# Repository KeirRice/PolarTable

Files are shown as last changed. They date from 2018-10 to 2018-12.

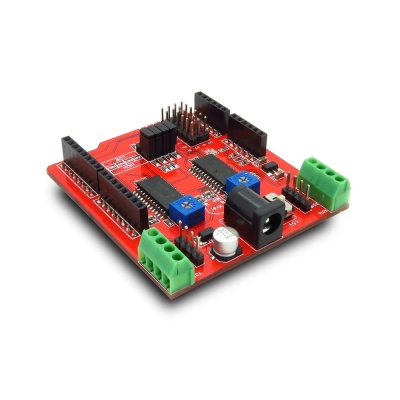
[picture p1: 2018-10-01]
Documents/Motor Shield/400px-ITEAD_DUAL_STEP_MOTOR_DRIVER_SHIELD.jpg

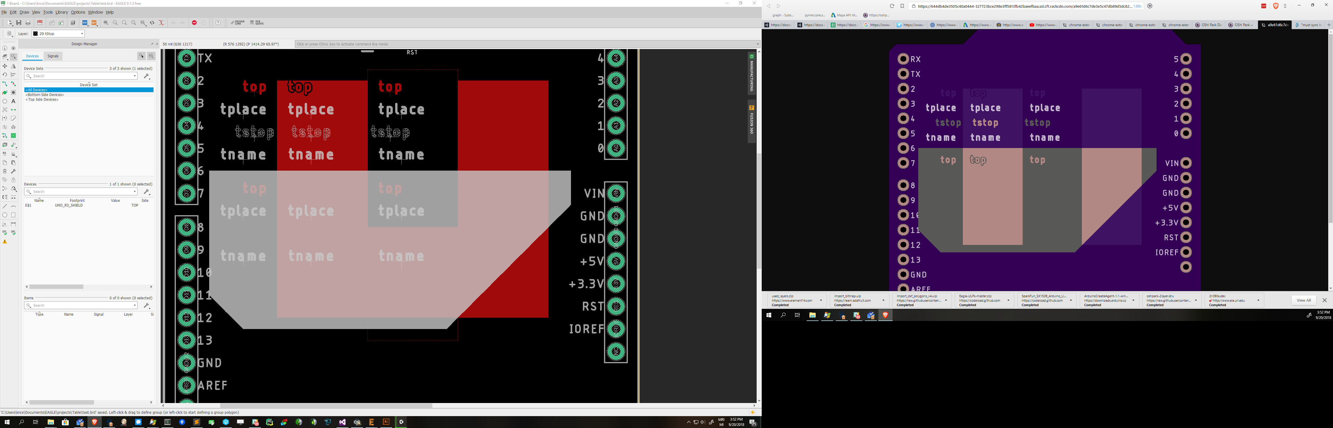
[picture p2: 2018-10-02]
Eagle/Images/Image 416.png

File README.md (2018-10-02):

# PolarTable

A colletion of design, code and art that is my journey towards making a physical table with a polor plotting system build in.

<p align="center">
  Polar Table Logo consisting of three rings braided togeather. Polar Table Logo
</p>

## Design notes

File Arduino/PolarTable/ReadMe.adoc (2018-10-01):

:Author: keir
:Email: keirrice@gmail.com
:Date: 18/09/2018
:Revision: version#
:License: Public Domain

= Project: {Project}

Describe your project

== Step 1: Installation
Please describe the steps to install this project.

For example:

1. Open this file
2. Edit as you like
3. Release to the World!

== Step 2: Assemble the circuit

Assemble the circuit following the diagram layout.png attached to the sketch

== Step 3: Load the code

Upload the code contained in this sketch on to your board

=== Folder structure

....
 sketch123                => Arduino sketch folder
  ├── sketch123.ino       => main Arduino file
  ├── schematics.png      => (optional) an image of the required schematics
  ├── layout.png          => (optional) an image of the layout
  └── ReadMe.adoc         => this file
....

=== License
This project is released under a {License} License.

=== Contributing
To contribute to this project please contact keir <keirrice@gmail.com>

=== BOM
Add the bill of the materials you need for this project.

|===
| ID | Part name      | Part number | Quantity
| R1 | 10k Resistor   | 1234-abcd   | 10       
| L1 | Red LED        | 2345-asdf   | 5        
| A1 | Arduino Zero   | ABX00066    | 1        
|===

=== Help
This document is written in the _AsciiDoc_ format, a markup language to describe documents. 
If you need help you can search the http://www.methods.co.nz/asciidoc[AsciiDoc homepage]
or consult the http://powerman.name/doc/asciidoc[AsciiDoc cheatsheet]

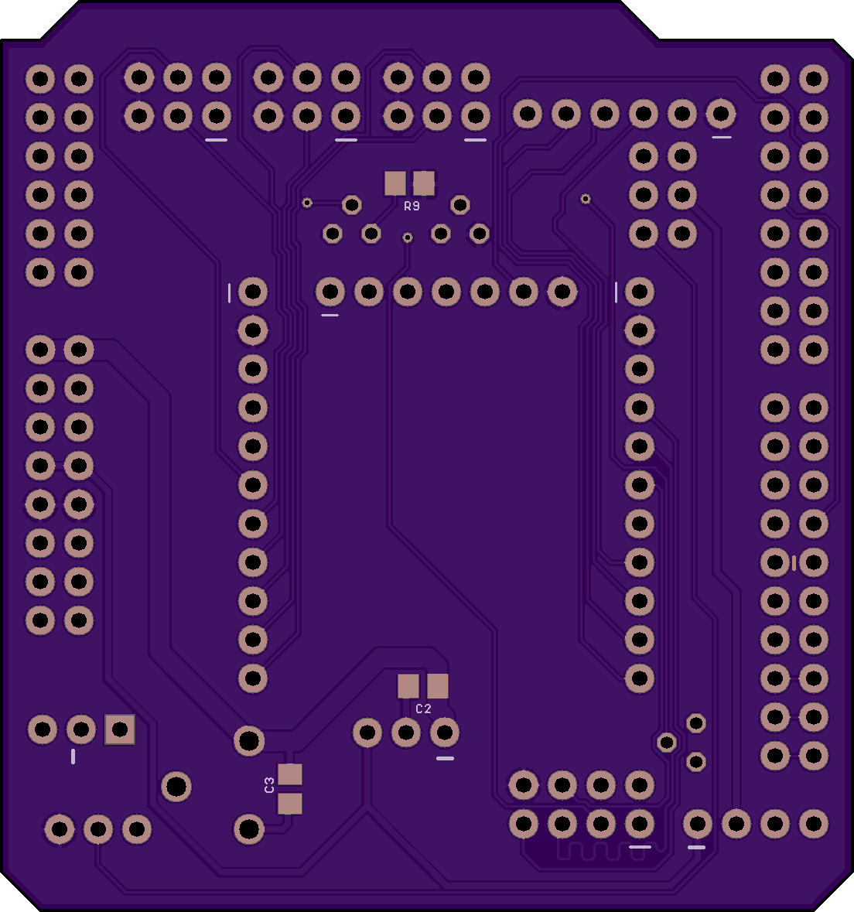
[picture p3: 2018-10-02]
Eagle/Images/0280e06795d403390924789a026d7050.png

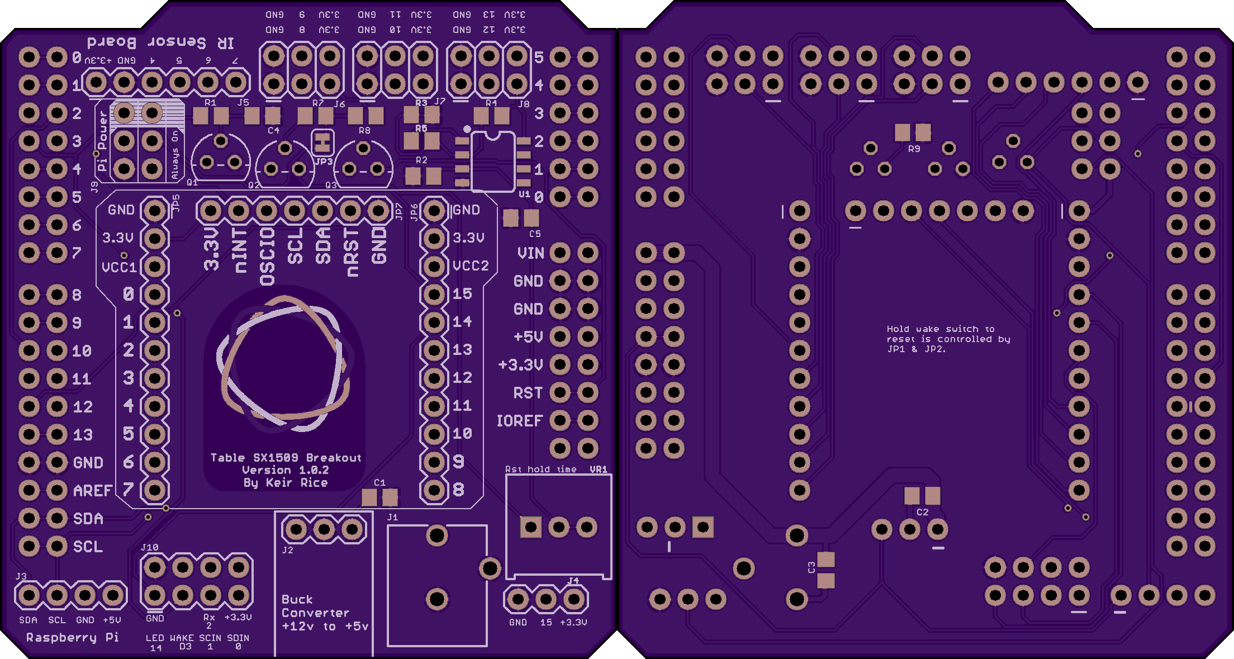
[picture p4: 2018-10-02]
Eagle/Images/72d867c8b2ec909129fff464216e762a.png

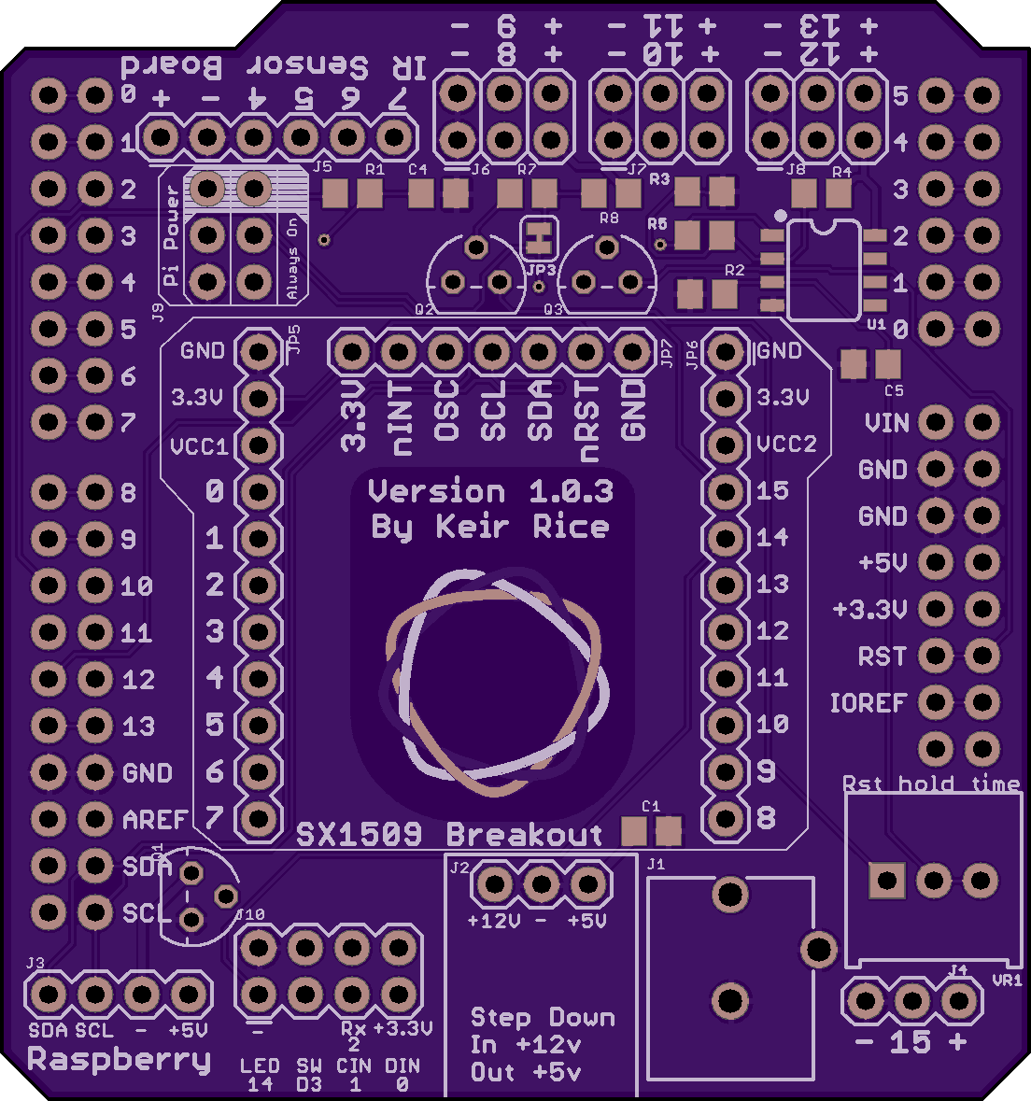
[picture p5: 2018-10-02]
Eagle/Images/a7a67751ff4bf5704754c66c1f886f41.png

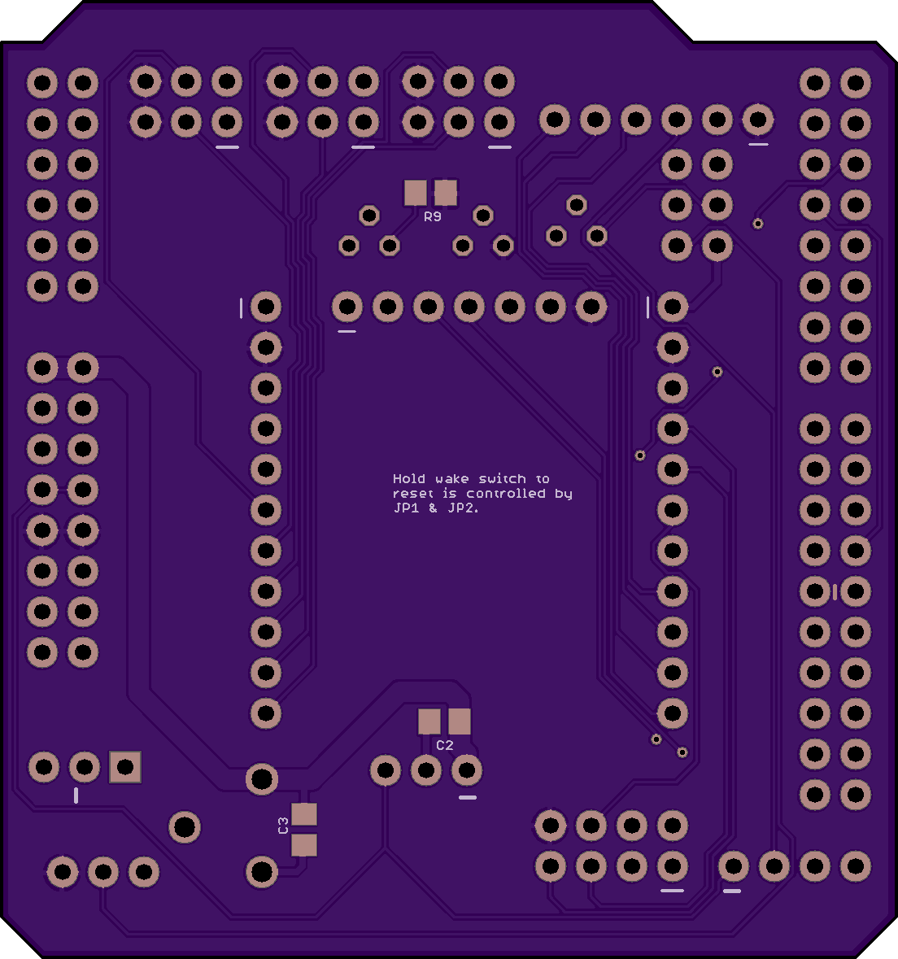
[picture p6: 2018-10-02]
Eagle/Images/8fd5240fe0b296190051bf0401c98b29 (1).png

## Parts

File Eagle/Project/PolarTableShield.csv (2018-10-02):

Part | Value | Device | Package | Description | NOTE | PROD_ID | SF_SKU | SPICEPREFIX | VALUE
B1 | Connect down to Arduino | ARDUINO_UNO_R3_SHIELDNOLABELS | UNO_R3_SHIELD_NOLABELS | Arduino R3 Shield Footprint
B2 | Connect up to motor shield | ARDUINO_UNO_R3_SHIELDNOLABELS | UNO_R3_SHIELD_NOLABELS | Arduino R3 Shield Footprint
C1 | 100u | CPOL-EUE2-5 | E2-5 | POLARIZED CAPACITOR, European symbol |  |  |  | C
C2 | 100u | CPOL-EUE2-5 | E2-5 | POLARIZED CAPACITOR, European symbol |  |  |  | C
C4 | 100nF | C-EUC0805 | C0805 | CAPACITOR, European symbol
C5 | 330uF | C-EUC0805 | C0805 | CAPACITOR, European symbol
C9 | 100n | C-EUC0805 | C0805 | CAPACITOR, European symbol |  |  |  | C
D1 | 1N5408 | 1N5408 | DO15-12 | DIODE
IC2 | LM358D | LM358D | SO08 | OP AMP also LM158; LM258; LM2904
J1 | Pi Power Jack | POWER_JACKPTH_BREAD | POWER_JACK_PTH_BREAD | Power Jack Connector |  | PRT-10811
J2 | Header - Right angled, female | CONN_031X03_2.54MM_RA_FEMALE | 1X03 | Multi connection point. Often used as Generic Header-pin footprint for 0.1 inch spaced/style header connections
J3 | Pi Connection | CONN_041X04_1.24MM_RA_MALE | 1X04_1.24MM_RA_MALE | Multi connection point. Often used as Generic Header-pin footprint for 0.1 inch spaced/style header connections
J4 |  | CONN_041X04_1.24MM_RA_MALE | 1X04_1.24MM_RA_MALE | Multi connection point. Often used as Generic Header-pin footprint for 0.1 inch spaced/style header connections
J5 | IR Sensors | CONN_06SILK_FEMALE_PTH | 1X06 | Multi connection point. Often used as Generic Header-pin footprint for 0.1 inch spaced/style header connections |  | CONN-08437
J6 | Switch A + B | CONN_03X22X03_2.54MM_RA_MALE | 2X3 | Multi connection point. Often used as Generic Header-pin footprint for 0.1 inch spaced/style header connections
J7 | Switch C + D | CONN_03X22X03_2.54MM_RA_MALE | 2X3 | Multi connection point. Often used as Generic Header-pin footprint for 0.1 inch spaced/style header connections
J8 | Switch E + F | CONN_03X22X03_2.54MM_RA_MALE | 2X3 | Multi connection point. Often used as Generic Header-pin footprint for 0.1 inch spaced/style header connections
J10 | LED + Radio | CONN_04X22X4_1.24MM_RA_MALE | 2X4 | Multi connection point. Often used as Generic Header-pin footprint for 0.1 inch spaced/style header connections
JP2 | Bypass Power Control | JUMPER-SMT_2_NO_SILK_ROUND | SMT-JUMPER_2_NO_SILK_ROUND | Normally open jumper
JP3 | Enable Hold to Reset | JUMPER-SMT_2_NC_TRACE_SILK | SMT-JUMPER_2_NC_TRACE_SILK | Normally closed trace jumper
JP4 | Route 15 to external | JUMPER-SMT_3_1-NC_TRACE_SILK | SMT-JUMPER_3_1-NC_TRACE_SILK | Normally closed trace jumper (1 of 2 connections)
JP5 |  | CONN_11 | 1X11 | Multi connection point. Often used as Generic Header-pin footprint for 0.1 inch spaced/style header connections
JP6 |  | CONN_11 | 1X11 | Multi connection point. Often used as Generic Header-pin footprint for 0.1 inch spaced/style header connections
JP7 |  | M07 | 1X07 | Header 7
Q1 | BC337 | BC337 | TO92 | NPN Transistor
Q2 | 2N3906 | 2N3906 | TO92D | PNP TRANSISTOR
Q3 | BC547 | BC547 | TO92 | NPN Transistor | Pull high until we get comparitor high output
R1 | 100 | R-US_R0805 | R0805 | RESISTOR, American symbol
R2 | 22.1k | R-US_R0805 | R0805 | RESISTOR, American symbol
R3 | 22k | R-US_R0805 | R0805 | RESISTOR, American symbol
R4 | 16.2k | R-US_R0805 | R0805 | RESISTOR, American symbol
R5 | 221k | R-US_R0805 | R0805 | RESISTOR, American symbol
R7 | 1k | R-US_R0805 | R0805 | RESISTOR, American symbol
R8 | 1k | R-US_R0805 | R0805 | RESISTOR, American symbol | Pull the switch high
R9 | 1k | R-US_R0805 | R0805 | RESISTOR, American symbol
U3 | SN74HC595DR | SN74HC595HCD | SO16 | 8-Bit Shift Register (Serial to Parallel) |  | IC-11325 |  |  | SN74HC165DR
VR1 | 10k | TRIMPOT-PTH-10MM-KNOB-1/2W-10% | TRIMPOT-PTH-3386U | Trimming Potentiometer (Trimpot) |  | RES-09730 | COM-09806 |  | 10k

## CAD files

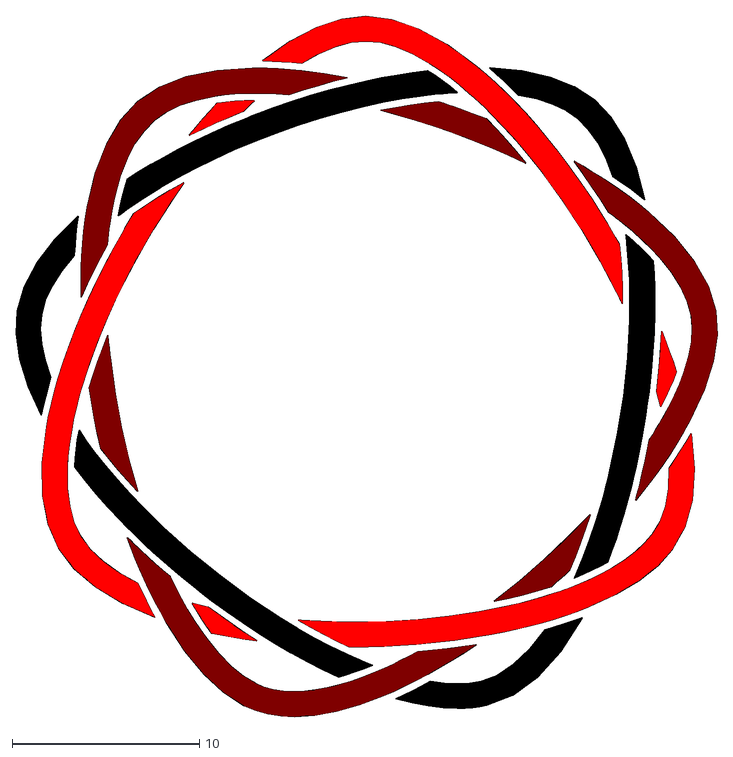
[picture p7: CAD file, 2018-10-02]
Eagle/Images/combined.dxf
37.4 x 37.4

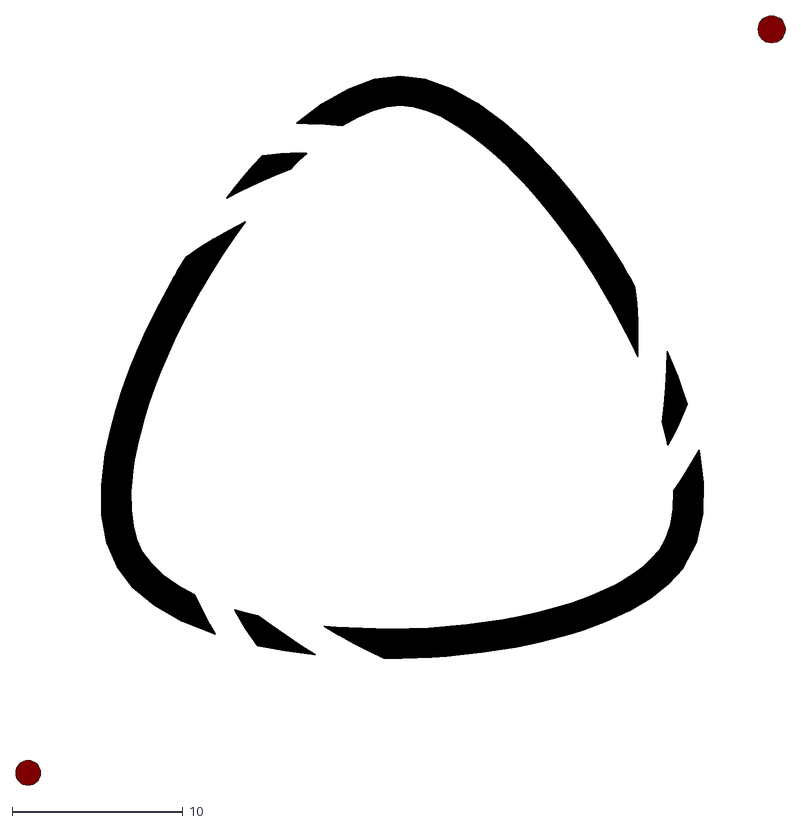
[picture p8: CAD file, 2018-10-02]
Eagle/Images/copper_pour.dxf
45.0 x 45.0

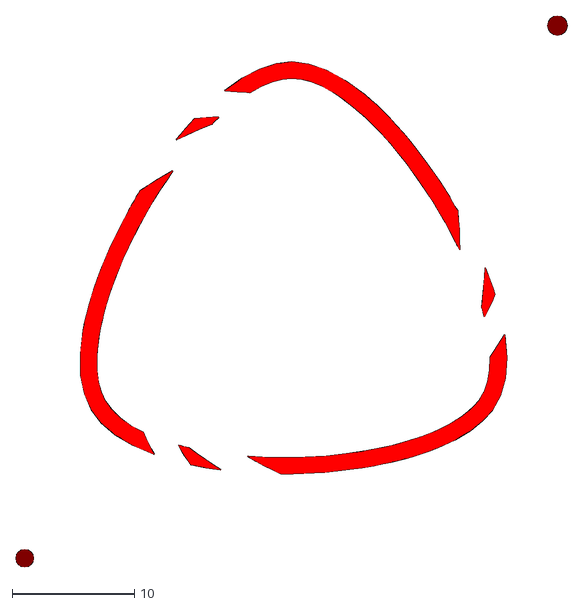
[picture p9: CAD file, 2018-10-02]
Eagle/Images/copper_stop.dxf
45.0 x 45.0

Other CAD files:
Python/turtle/Samples/heart.dwg
Eagle/Images/copper.dwg
Fusion360/Table.f3z

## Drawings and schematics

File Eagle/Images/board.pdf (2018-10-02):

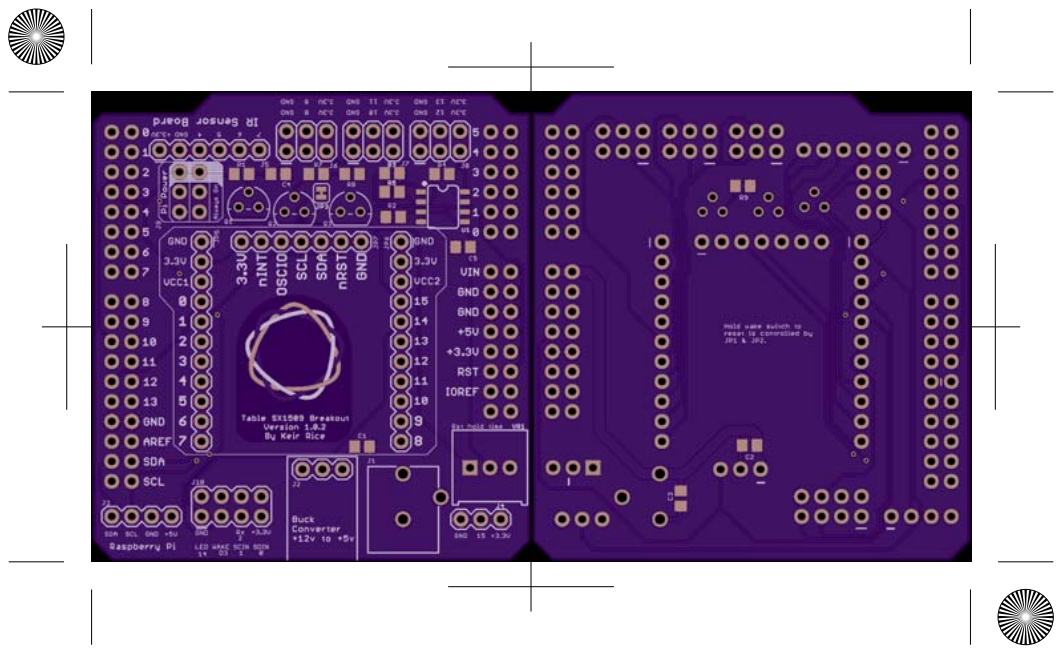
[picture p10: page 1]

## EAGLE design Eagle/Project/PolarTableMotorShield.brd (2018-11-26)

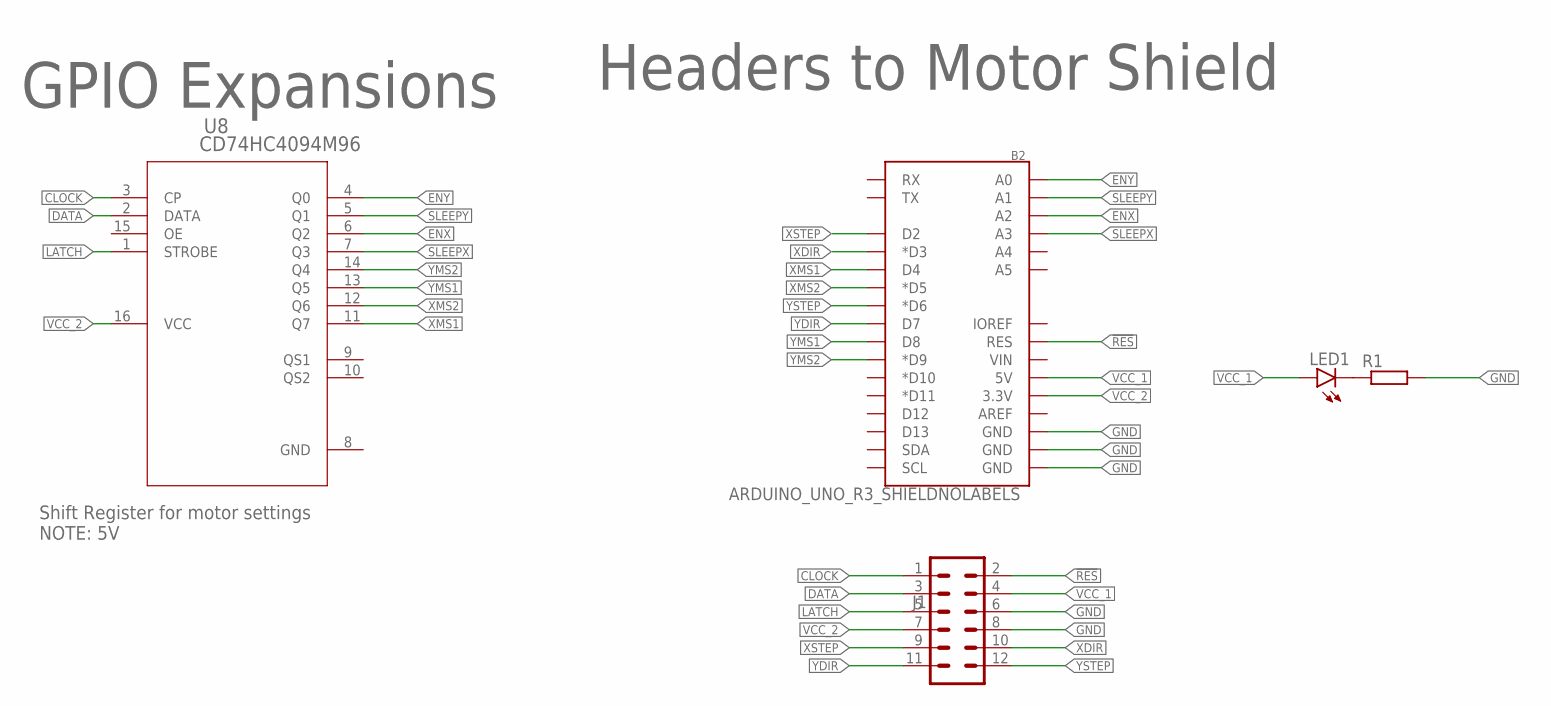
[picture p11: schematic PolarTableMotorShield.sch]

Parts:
B2: ARDUINO_UNO_R3_SHIELDNOLABELS; UNO_R3_SHIELD_NOLABELS
J1: CONN_06X21.24MM_RA_MALE; 2X6
LED1: LEDCHIPLED_0805; CHIPLED_0805
R1: R-EU_R0805; R0805
U8: CD74HC4094M96; D16

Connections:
!RES: B2.RES, J1.2
CLOCK: J1.1, U8.3 (CP)
DATA: J1.3, U8.2 (DATA)
ENX: B2.A2, U8.6 (Q2)
ENY: B2.A0, U8.4 (Q0)
GND: B2.GND@0 (GND), B2.GND@1 (GND), B2.GND@2 (GND), J1.6, J1.8, R1.2, U8.8 (GND)
LATCH: J1.5, U8.1 (STROBE)
unnamed: LED1.C, R1.1
SLEEPX: B2.A3, U8.7 (Q3)
SLEEPY: B2.A1, U8.5 (Q1)
VCC_1: B2.5V, J1.4, LED1.A
VCC_2: B2.3.3V, J1.7, U8.16 (VCC)
XDIR: B2.D3 (*D3), J1.10
XMS1: B2.D4, U8.11 (Q7)
XMS2: B2.D5 (*D5), U8.12 (Q6)
XSTEP: B2.D2, J1.9
YDIR: B2.D7, J1.11
YMS1: B2.D8, U8.13 (Q5)
YMS2: B2.D9 (*D9), U8.14 (Q4)
YSTEP: B2.D6 (*D6), J1.12

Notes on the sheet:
GPIO Expansions
Shift Register for motor settings NOTE: 5V
Headers to Motor Shield

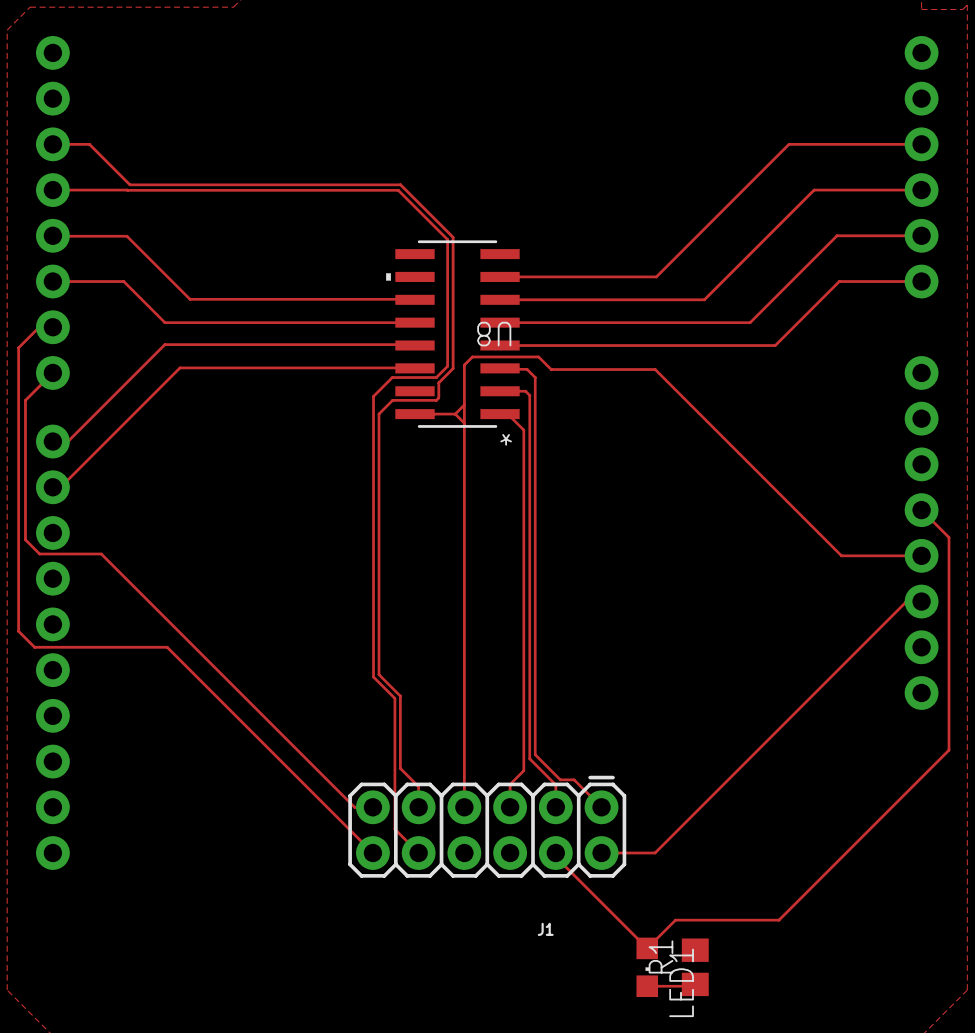
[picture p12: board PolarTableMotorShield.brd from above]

Board: 2 copper layers, 5 parts (0 on the bottom side), 20 nets.

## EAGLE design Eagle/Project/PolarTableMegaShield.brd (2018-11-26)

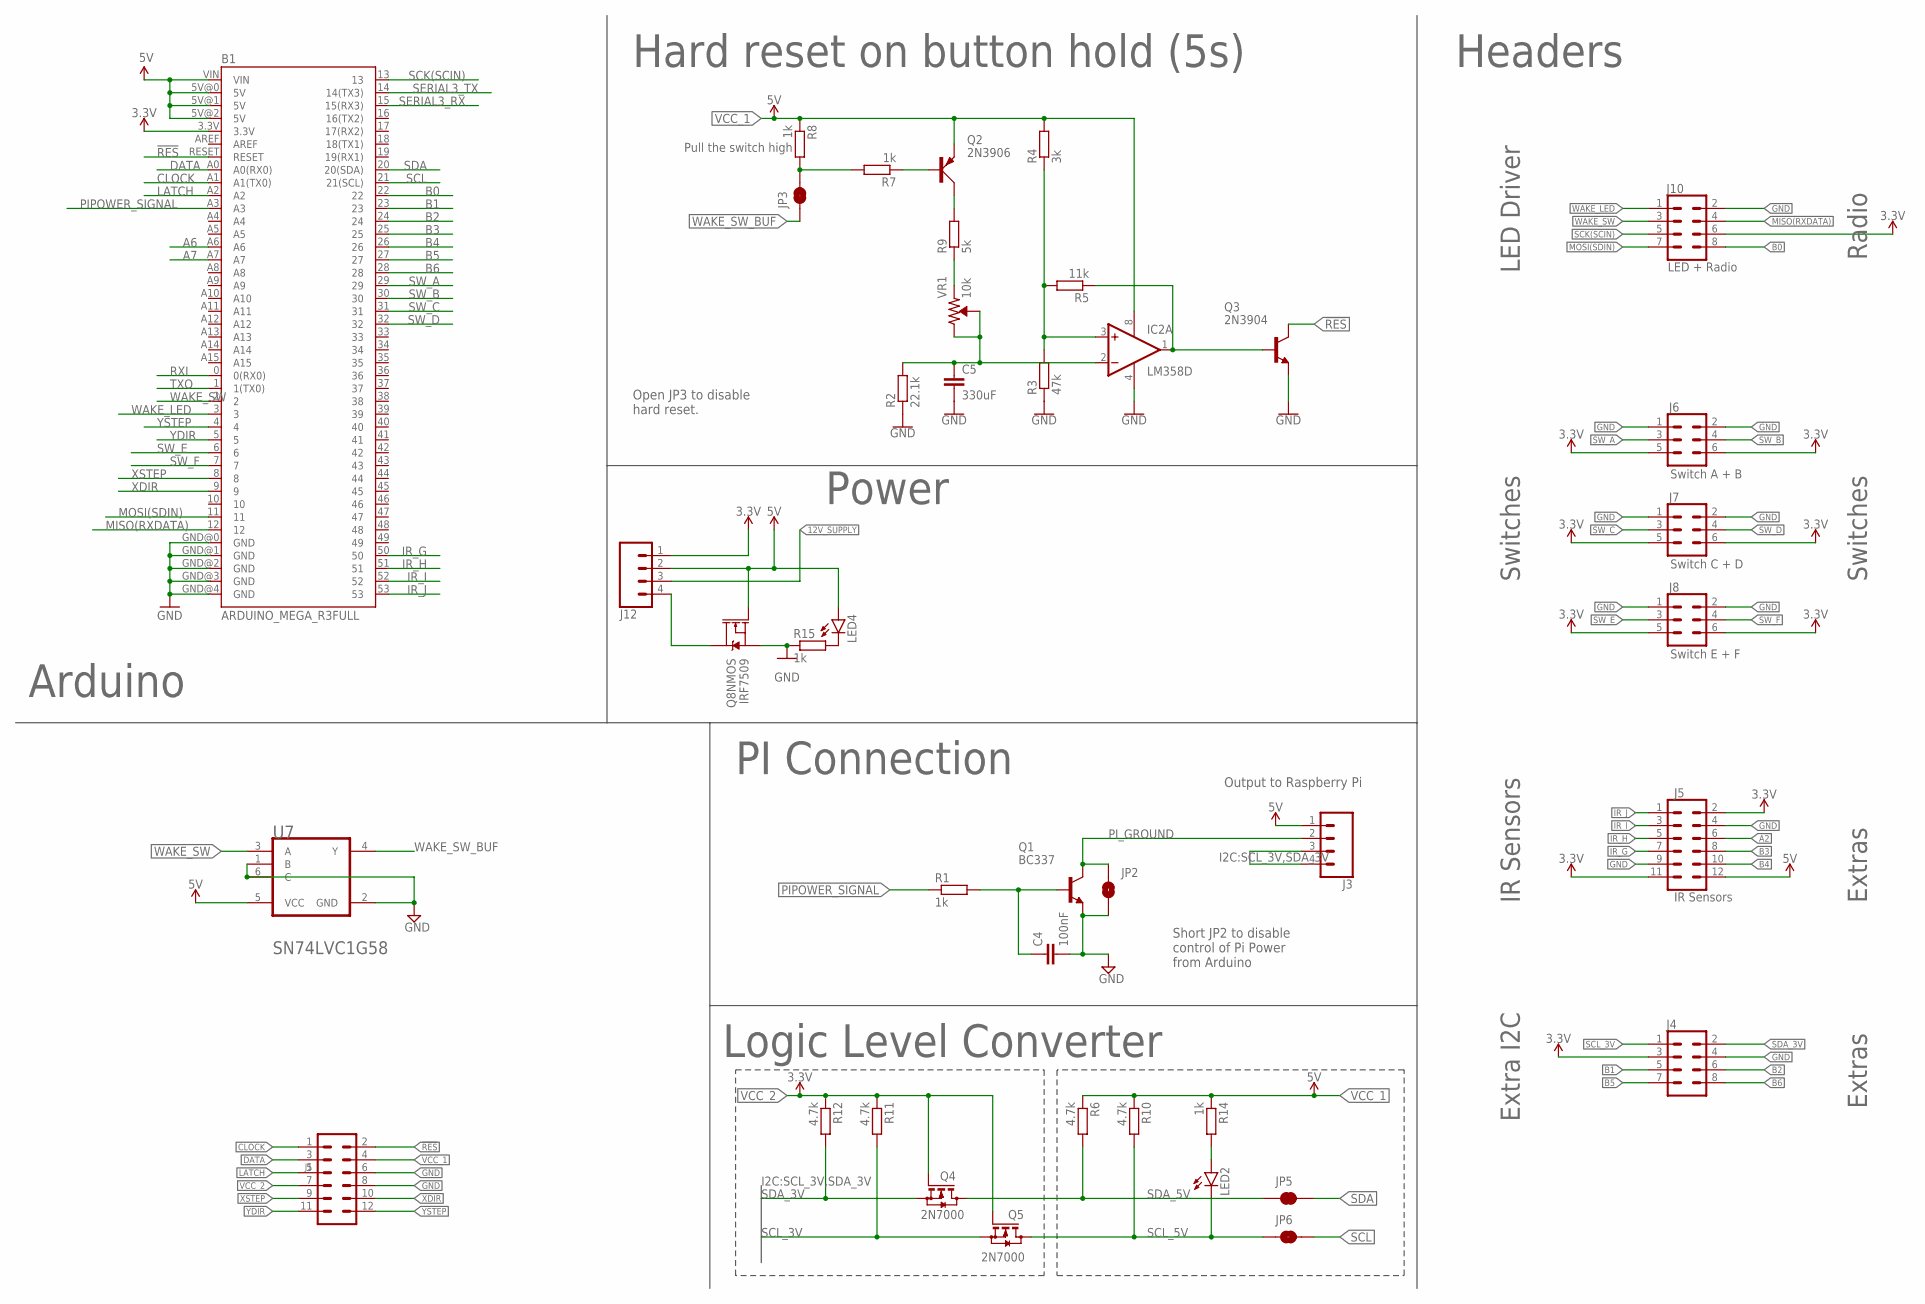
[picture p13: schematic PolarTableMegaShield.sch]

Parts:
B1: ARDUINO_MEGA_R3FULL; ARDUINO_MEGA
C4: 100nF; C0805
C5: 330uF; C0805
IC2: LM358D; SO08
J1: CONN_06X21.24MM_RA_MALE; 2X6
J3: Pi Connection; 1X04_1.24MM_RA_MALE
J4: CONN_04X22X4_1.24MM_RA_MALE; 2X4
J5: IR Sensors; 2X6
J6: Switch A + B; 2X3
J7: Switch C + D; 2X3
J8: Switch E + F; 2X3
J10: LED + Radio; 2X4
J12: CONN_04JST-PTH; JST-4-PTH
JP2: JUMPER-SMT_2_NO_SILK; SMT-JUMPER_2_NO_SILK
JP3: Enable Hold to Reset; SMT-JUMPER_2_NC_TRACE_SILK
JP5, JP6: JUMPER-SMT_2_NC_TRACE_NO-SILK; SMT-JUMPER_2_NC_TRACE_NO-SILK
LED2, LED4: LEDCHIP-LED0805; CHIP-LED0805
Q1: BC337; TO92
Q2: 2N3906; TO92D
Q3: 2N3904; TO92
Q4, Q5: 2N7000; TO92-
Q8: IRF7509; MSOP8
R1, R7, R8, R14, R15: 1k; M0805
R2: 22.1k; M0805
R3: 47k; M0805
R4: 3k; M0805
R5: 11k; M0805
R6, R10, R11, R12: 4.7k; M0805
R9: 5k; M0805
U7: Buffer; SOT363_PHILIPS
VR1: 10k; TRIMPOT-PTH-3386U

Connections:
12V_SUPPLY: J12.3
!RES: B1.RESET, J1.2, Q3.1 (C)
$N99: JP3.2, R7.2, R8.2
A2: J5.6
A6: B1.A6
A7: B1.A7
B0: B1.22, J10.8
B1: B1.23, J4.5
B2: B1.24, J4.6
B3: B1.25, J5.8
B4: B1.26, J5.10
B5: B1.27, J4.7
B6: B1.28, J4.8
CLOCK: B1.A1 (A1(TX0)), J1.1
COMP_OUT: IC2.1 (OUT), Q3.2 (B), R5.1
DATA: B1.A0 (A0(RX0)), J1.3
GND: B1.GND@0 (GND), B1.GND@1 (GND), B1.GND@2 (GND), B1.GND@3 (GND), B1.GND@4 (GND), C4.2, C5.2, IC2.4 (V-), J1.6, J1.8, J4.4, J5.4, J5.9, J6.1, J6.2, J7.1, J7.2, J8.1, J8.2, J10.2, JP2.2, Q1.1 (E), Q3.3 (E), Q8.1 (S), R2.1, R3.1, R15.1, U7.1 (B), U7.2 (GND), U7.6 (C)
IR_G: B1.50, J5.7
IR_H: B1.51, J5.5
IR_I: B1.52, J5.3
IR_J: B1.53, J5.1
LATCH: B1.A2, J1.5
MISO(RXDATA): B1.12, J10.4
MOSI(SDIN): B1.11, J10.7
unnamed: Q2.B, R7.1
unnamed: C4.1, Q1.2 (B), R1.2
unnamed: Q2.C, R9.2
unnamed: J12.4, Q8.7 (D), Q8.8 (D)
unnamed: IC2.3 (+IN), R3.2, R4.1, R5.2
unnamed: R9.1, VR1.1 (CCW)
unnamed: C5.1, IC2.2 (-IN), R2.2, VR1.2 (WIPER), VR1.3 (CW)
unnamed: LED4.C, R15.2
unnamed: LED2.A, R14.2
PIPOWER_SIGNAL: B1.A3, R1.1
PI_GROUND: J3.2, JP2.1, Q1.3 (C)
RXI: B1.0 (0(RX0))
SCK(SCIN): B1.13, J10.5
SCL: B1.21 (21(SCL)), JP6.2
SCL_3V: J3.3, J4.1, Q5.1 (S), R11.2
SCL_5V: JP6.1, LED2.C, Q5.3 (D), R10.2
SDA: B1.20 (20(SDA)), JP5.2
SDA_3V: J3.4, J4.2, Q4.1 (S), R12.2
SDA_5V: JP5.1, Q4.3 (D), R6.2
SERIAL3_RX: B1.15 (15(RX3))
SERIAL3_TX: B1.14 (14(TX3))
SW_A: B1.29, J6.3
SW_B: B1.30, J6.4
SW_C: B1.31, J7.3
SW_D: B1.32, J7.4
SW_E: B1.6, J8.3
SW_F: B1.7, J8.4
TXO: B1.1 (1(TX0))
VCC_1: B1.5V@0 (5V), B1.5V@1 (5V), B1.5V@2 (5V), B1.VIN, IC2.8 (V+), J1.4, J3.1, J5.12, J12.2, LED4.A, Q2.E, Q8.2 (G), R4.2, R6.1, R8.1, R10.1, R14.1, U7.5 (VCC)
VCC_2: B1.3.3V, J1.7, J4.3, J5.2, J5.11, J6.5, J6.6, J7.5, J7.6, J8.5, J8.6, J10.6, J12.1, Q4.2 (G), Q5.2 (G), R11.1, R12.1
WAKE_LED: B1.3, J10.1
WAKE_SW: B1.2, J10.3, U7.3 (A)
WAKE_SW_BUF: JP3.1, U7.4 (Y)
XDIR: B1.9, J1.10
XSTEP: B1.8, J1.9
YDIR: B1.5, J1.11
YSTEP: B1.4, J1.12

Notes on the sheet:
PI Connection
LED Driver
IR Sensors
Switches
Radio
Hard reset on button hold (5s)
Power
Logic Level Converter
Extras
Extra I2C
Arduino
Headers
Output to Raspberry Pi
Short JP2 to disable control of Pi Power from Arduino
Open JP3 to disable hard reset.

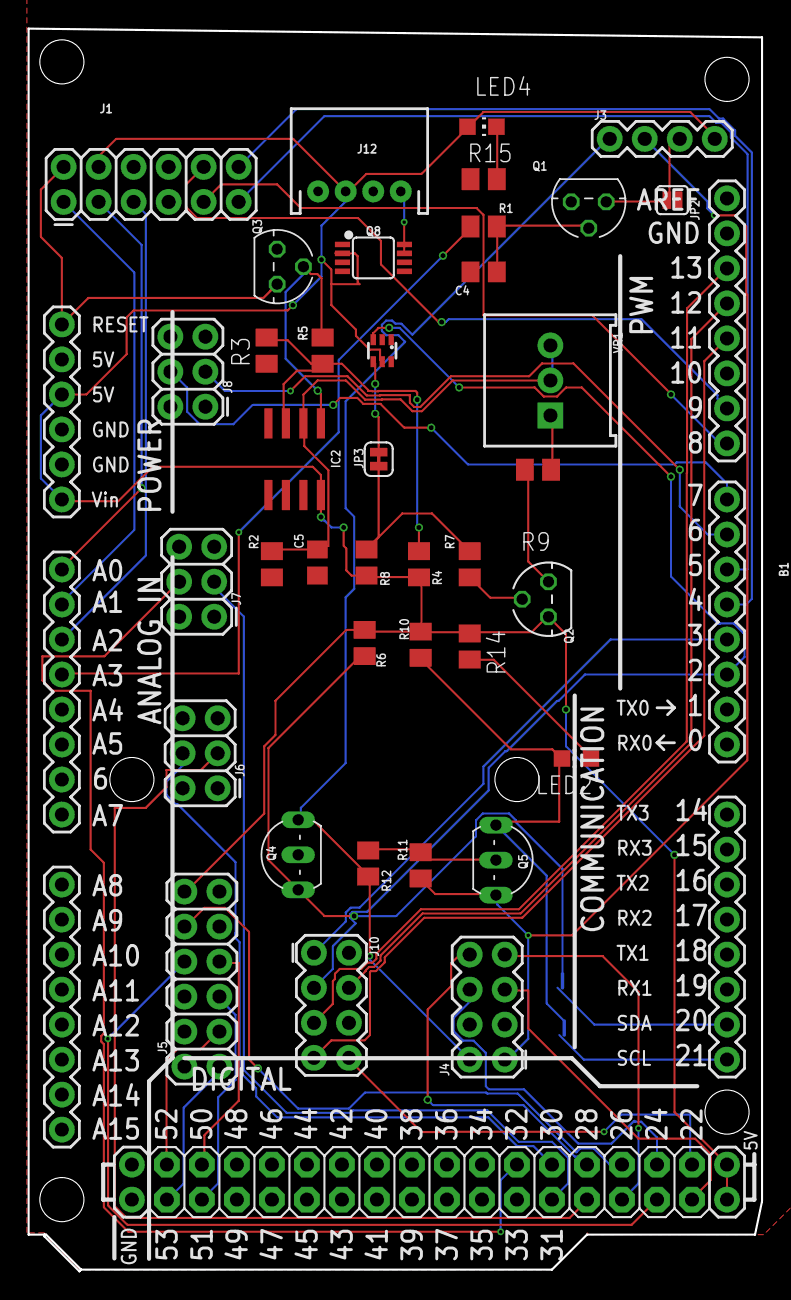
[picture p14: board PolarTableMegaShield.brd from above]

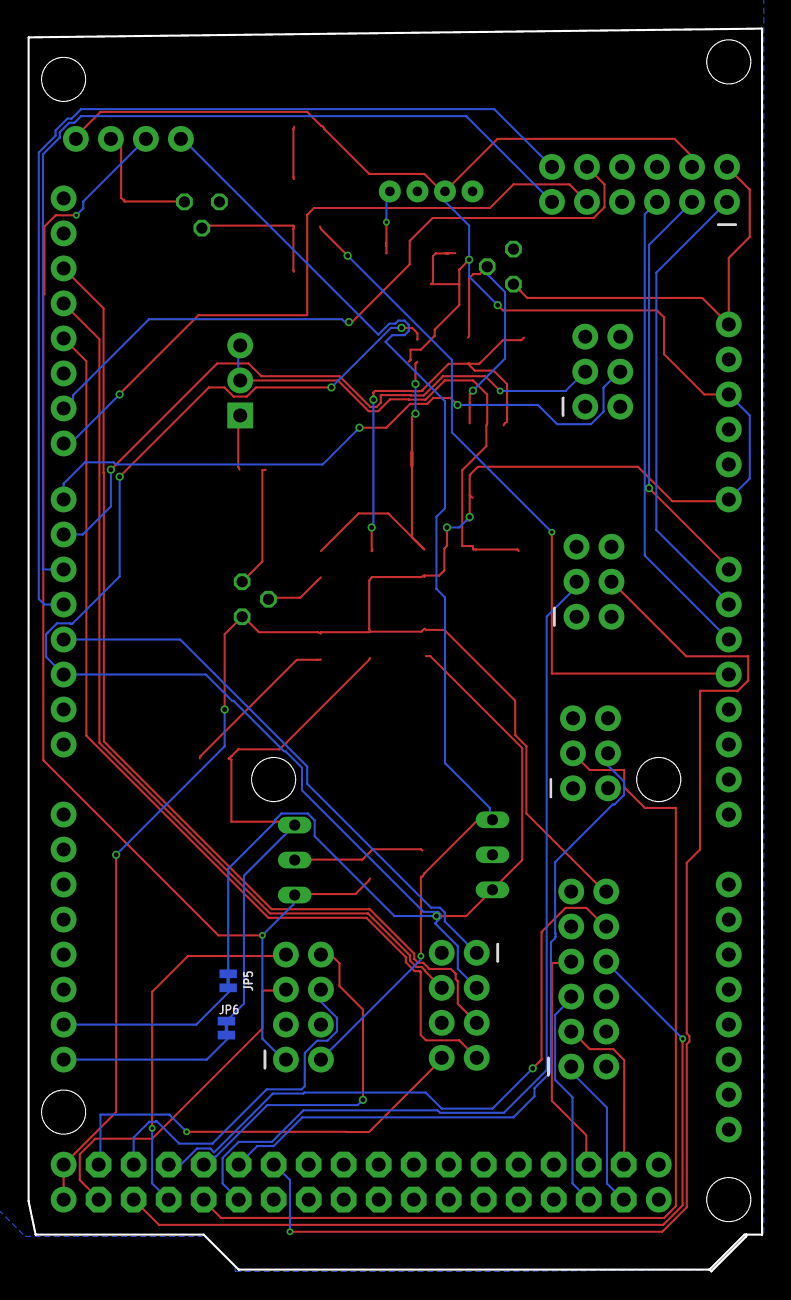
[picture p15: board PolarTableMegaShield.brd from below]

Board: 2 copper layers, 53.2 x 90.2 mm, 41 parts (2 on the bottom side), 53 nets.

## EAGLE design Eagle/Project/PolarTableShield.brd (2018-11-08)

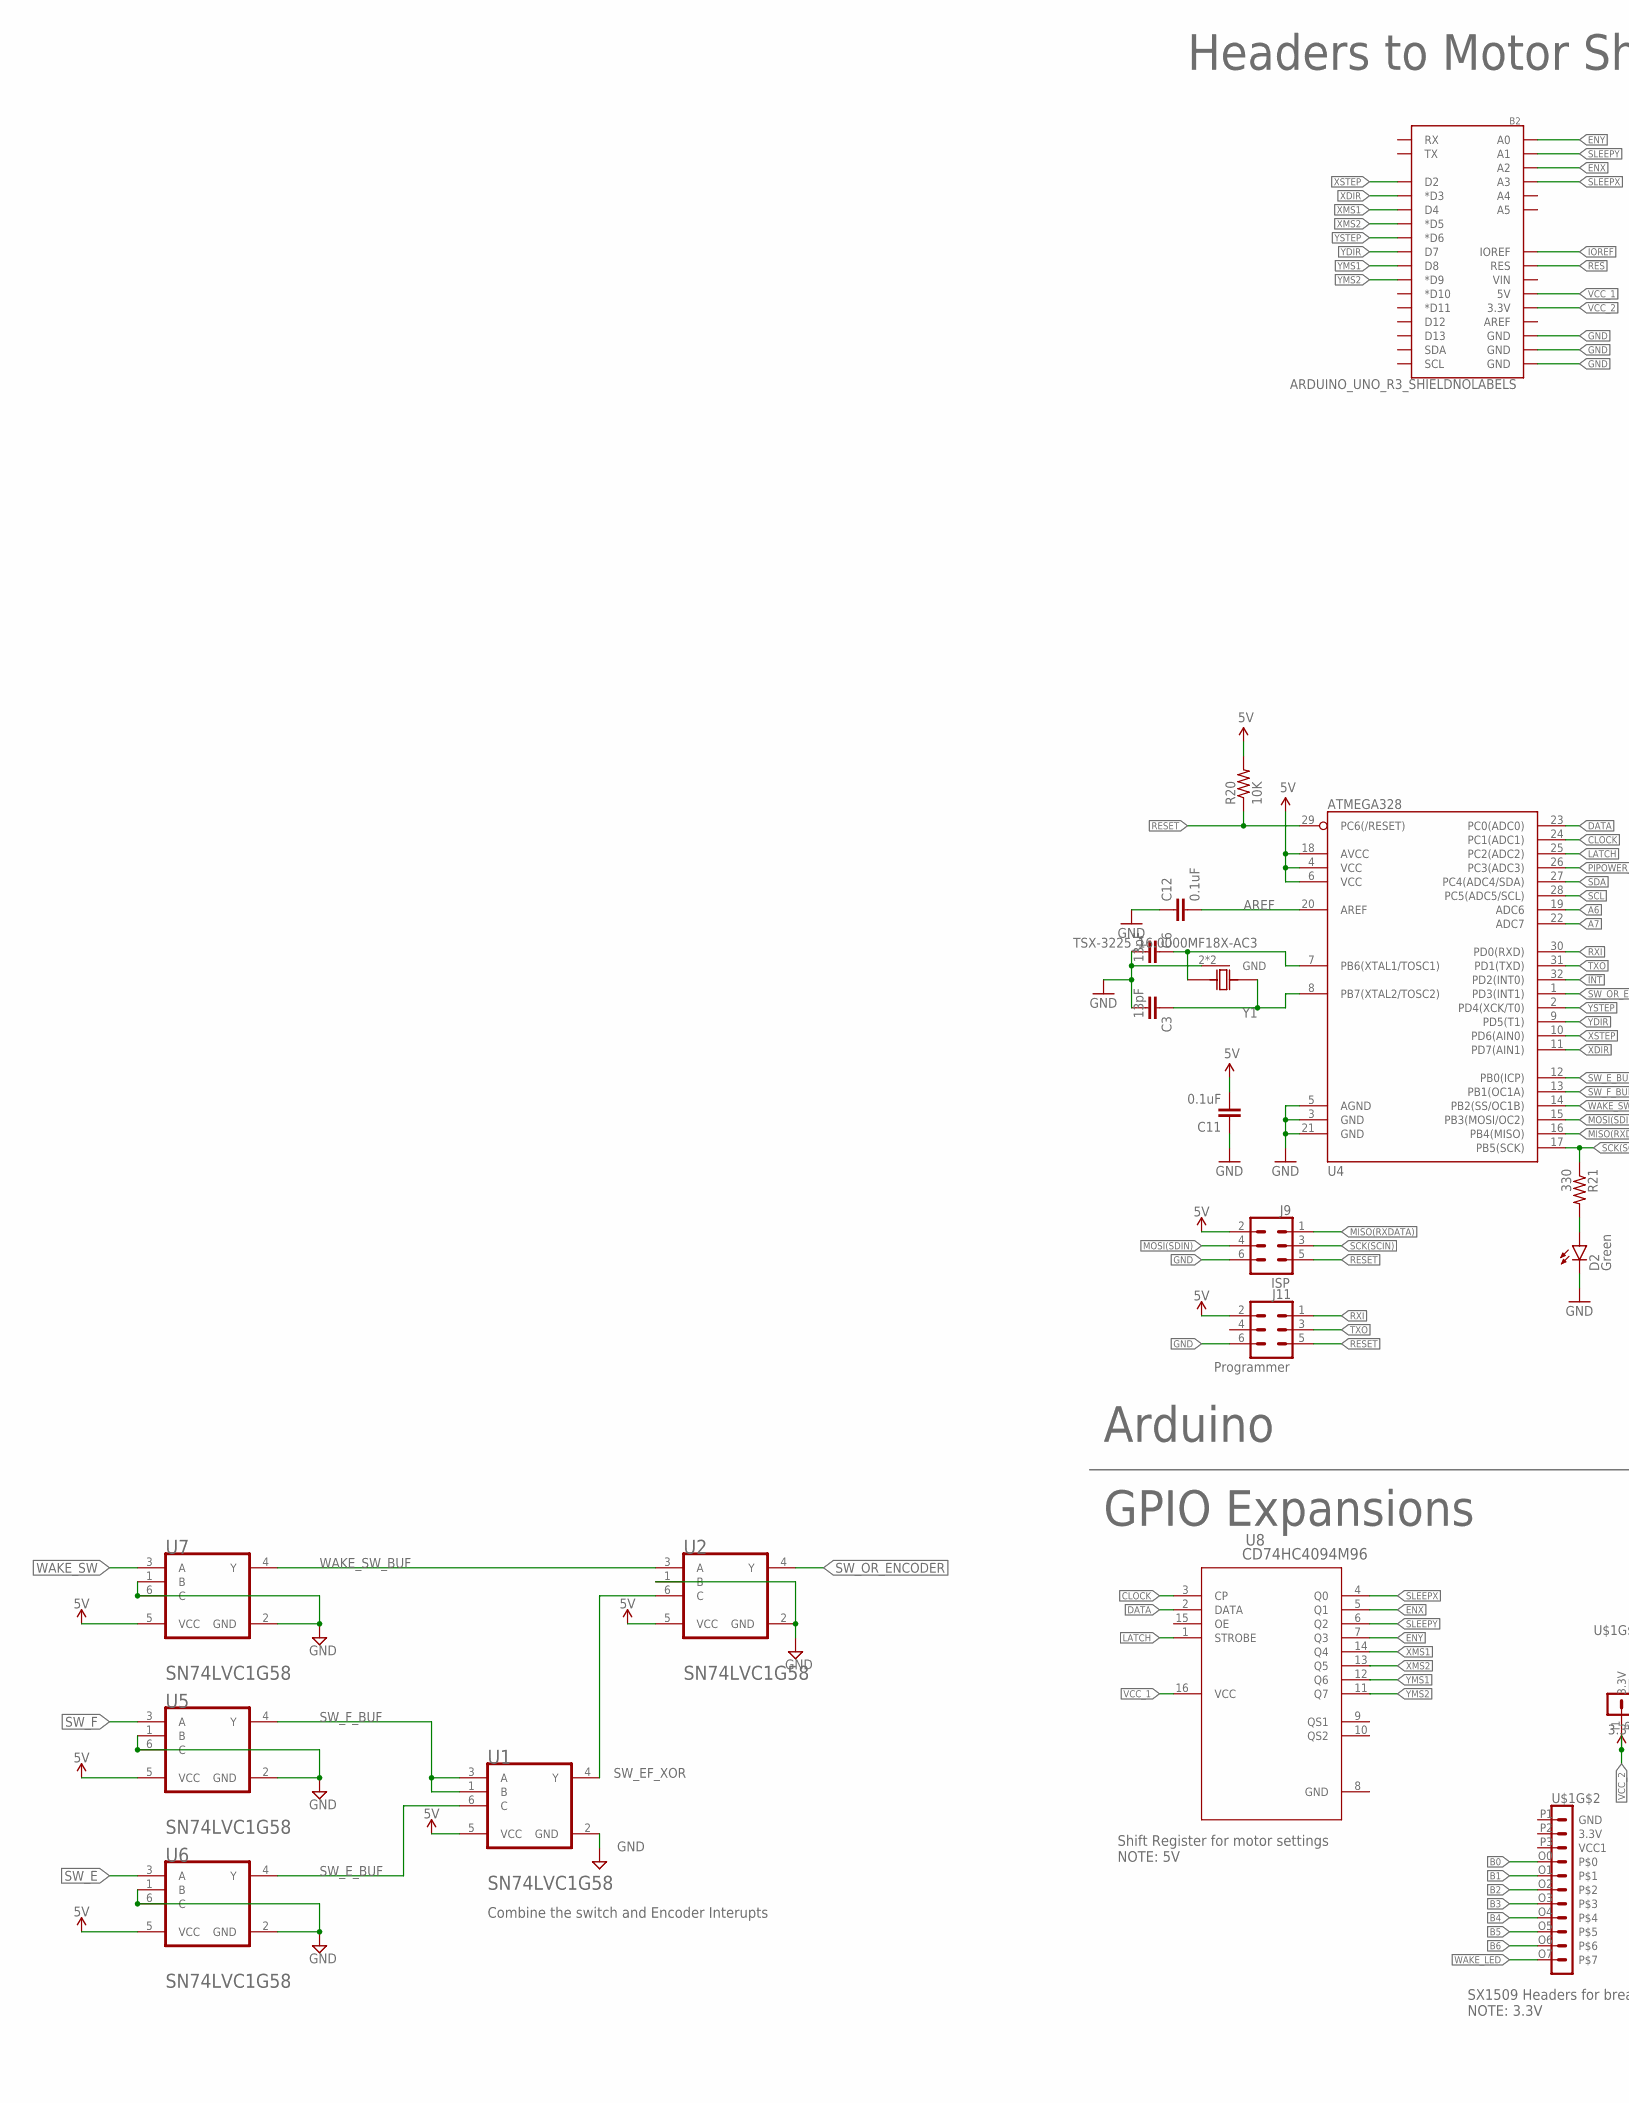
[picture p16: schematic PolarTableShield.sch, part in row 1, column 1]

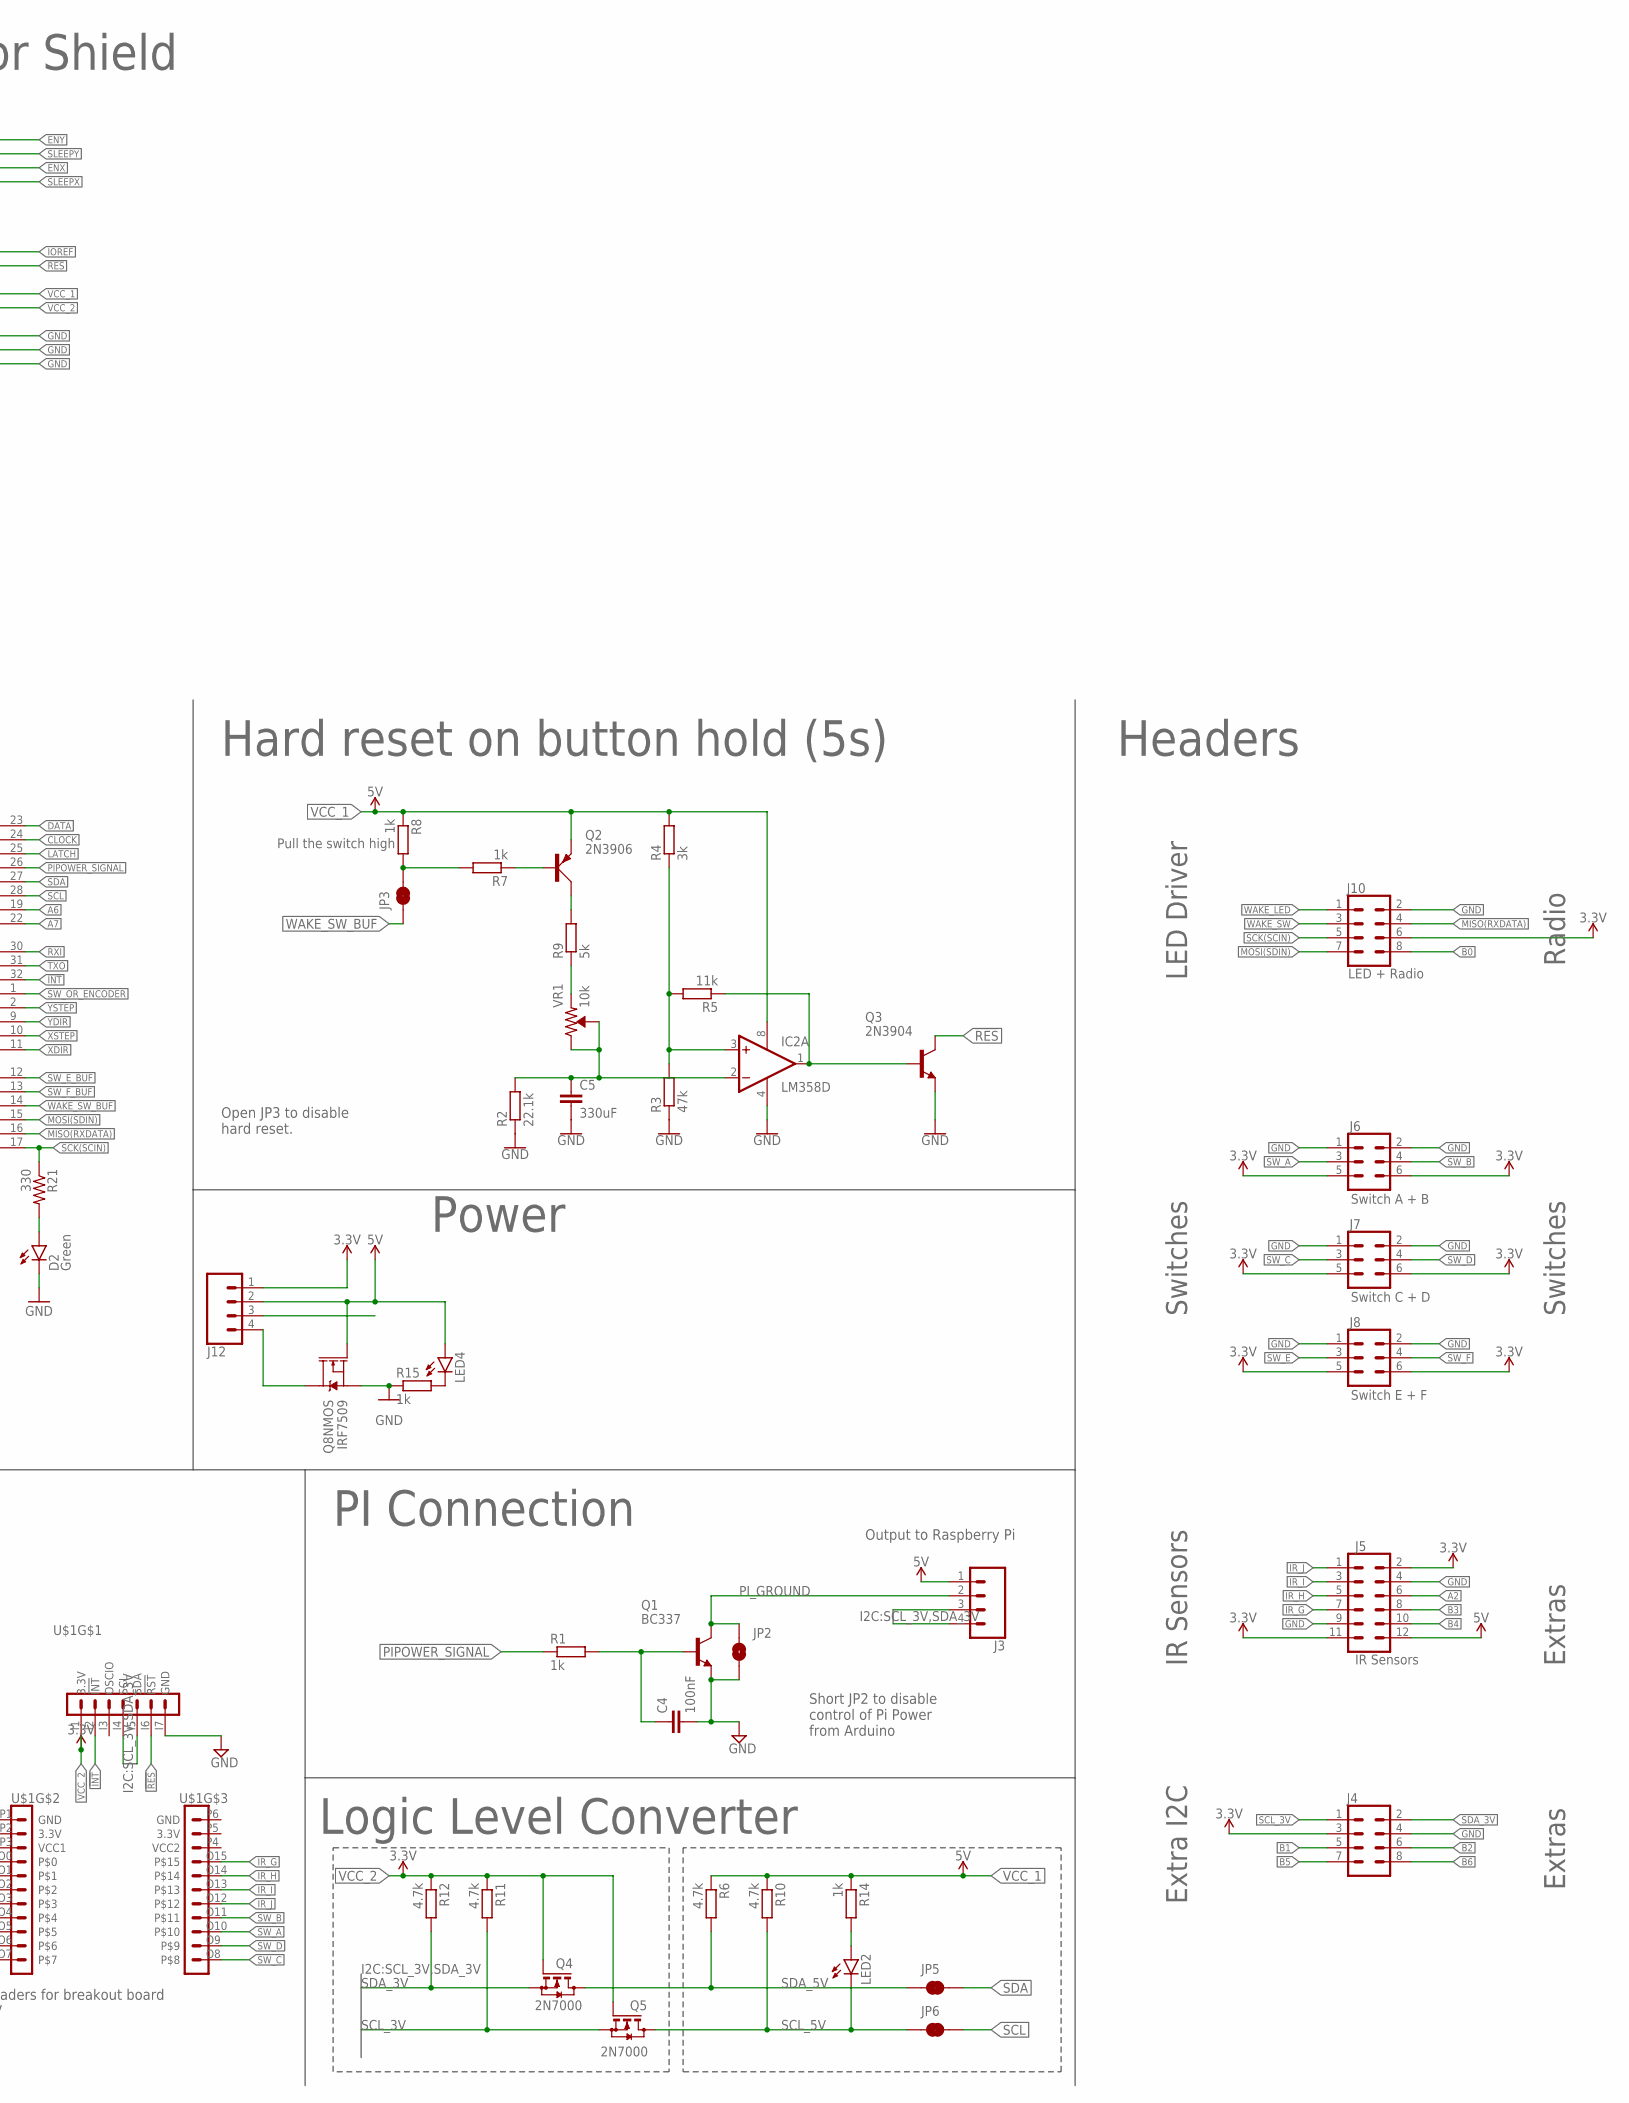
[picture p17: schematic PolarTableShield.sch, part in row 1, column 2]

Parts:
B2: ARDUINO_UNO_R3_SHIELDNOLABELS; UNO_R3_SHIELD_NOLABELS
C3, C6: 13pF; 0603-CAP
C4: 100nF; C0805
C5: 330uF; C0805
C11, C12: 0.1uF; 0603-CAP
D2: Green; CHIP-LED0805
IC2: LM358D; SO08
J3: Pi Connection; 1X04_1.24MM_RA_MALE
J4: CONN_04X22X4_1.24MM_RA_MALE; 2X4
J5: IR Sensors; 2X6
J6: Switch A + B; 2X3
J7: Switch C + D; 2X3
J8: Switch E + F; 2X3
J9: ISP; 2X3-NS
J10: LED + Radio; 2X4
J11: Programmer; 2X3-NS
J12: CONN_04JST-PTH; JST-4-PTH
JP2: JUMPER-SMT_2_NO_SILK; SMT-JUMPER_2_NO_SILK
JP3: Enable Hold to Reset; SMT-JUMPER_2_NC_TRACE_SILK
JP5, JP6: JUMPER-SMT_2_NC_TRACE_NO-SILK; SMT-JUMPER_2_NC_TRACE_NO-SILK
LED2, LED4: LEDCHIP-LED0805; CHIP-LED0805
Q1: BC337; TO92
Q2: 2N3906; TO92D
Q3: 2N3904; TO92
Q4, Q5: 2N7000; TO92-
Q8: IRF7509; MSOP8
R1, R7, R8, R14, R15: 1k; M0805
R2: 22.1k; M0805
R3: 47k; M0805
R4: 3k; M0805
R5: 11k; M0805
R6, R10, R11, R12: 4.7k; M0805
R9: 5k; M0805
R20: 10K; 0603-RES
R21: 330; 0603-RES
U1: XOR; SOT363_PHILIPS
U2: OR; SOT363_PHILIPS
U4: ATMEGA328; TQFP32-08
U5, U6, U7: Buffer; SOT363_PHILIPS
U8: CD74HC4094M96; D16
U$1: SX1509
VR1: 10k; TRIMPOT-PTH-3386U
Y1: TSX-3225_16.0000MF18X-AC3; XTAL_TSX-3225_16.0000MF18X-AC3

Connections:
12V_SUPPLY: J12.3
!INT: U4.32 (PD2(INT0)), U$1.I2 (!INT)
!RES: B2.RES, Q3.1 (C), U$1.I6 (!RST)
$N99: JP3.2, R7.2, R8.2
A2: J5.6
A6: U4.19 (ADC6)
A7: U4.22 (ADC7)
AREF: C12.2, U4.20 (AREF)
B0: J10.8, U$1.O0
B1: J4.5, U$1.O1
B2: J4.6, U$1.O2
B3: J5.8, U$1.O3
B4: J5.10, U$1.O4
B5: J4.7, U$1.O5
B6: J4.8, U$1.O6
CLOCK: U4.24 (PC1(ADC1)), U8.3 (CP)
COMP_OUT: IC2.1 (OUT), Q3.2 (B), R5.1
DATA: U4.23 (PC0(ADC0)), U8.2 (DATA)
ENX: B2.A2, U8.5 (Q1)
ENY: B2.A0, U8.7 (Q3)
GND: B2.GND@0 (GND), B2.GND@1 (GND), B2.GND@2 (GND), C3.2, C4.2, C5.2, C6.2, C11.1, C12.1, D2.C, IC2.4 (V-), J4.4, J5.4, J5.9, J6.1, J6.2, J7.1, J7.2, J8.1, J8.2, J9.6, J10.2, J11.6, JP2.2, Q1.1 (E), Q3.3 (E), Q8.1 (S), R2.1, R3.1, R15.1, U1.2 (GND), U2.1 (B), U2.2 (GND), U4.3 (GND), U4.5 (AGND), U4.21 (GND), U5.1 (B), U5.2 (GND), U5.6 (C), U6.1 (B), U6.2 (GND), U6.6 (C), U7.1 (B), U7.2 (GND), U7.6 (C), U8.8 (GND), U$1.I7 (GND), Y1.2 (GND), Y1.4 (GND)
IOREF: B2.IOREF
IR_G: J5.7, U$1.O15
IR_H: J5.5, U$1.O14
IR_I: J5.3, U$1.O13
IR_J: J5.1, U$1.O12
LATCH: U4.25 (PC2(ADC2)), U8.1 (STROBE)
MISO(RXDATA): J9.1, J10.4, U4.16 (PB4(MISO))
MOSI(SDIN): J9.4, J10.7, U4.15 (PB3(MOSI/OC2))
unnamed: Q2.B, R7.1
unnamed: C4.1, Q1.2 (B), R1.2
unnamed: Q2.C, R9.2
unnamed: J12.4, Q8.7 (D), Q8.8 (D)
unnamed: IC2.3 (+IN), R3.2, R4.1, R5.2
unnamed: R9.1, VR1.1 (CCW)
unnamed: C3.1, U4.8 (PB7(XTAL2/TOSC2)), Y1.1
unnamed: C5.1, IC2.2 (-IN), R2.2, VR1.2 (WIPER), VR1.3 (CW)
unnamed: LED4.C, R15.2
unnamed: LED2.A, R14.2
unnamed: D2.A, R21.2
unnamed: C6.1, U4.7 (PB6(XTAL1/TOSC1)), Y1.3
PIPOWER_SIGNAL: R1.1, U4.26 (PC3(ADC3))
PI_GROUND: J3.2, JP2.1, Q1.3 (C)
RESET: J9.5, J11.5, R20.1, U4.29 (PC6(/RESET))
RXI: J11.1, U4.30 (PD0(RXD))
SCK(SCIN): J9.3, J10.5, R21.1, U4.17 (PB5(SCK))
SCL: JP6.2, U4.28 (PC5(ADC5/SCL))
SCL_3V: J3.3, J4.1, Q5.1 (S), R11.2, U$1.I4 (SCL)
SCL_5V: JP6.1, LED2.C, Q5.3 (D), R10.2
SDA: JP5.2, U4.27 (PC4(ADC4/SDA))
SDA_3V: J3.4, J4.2, Q4.1 (S), R12.2, U$1.I5 (SDA)
SDA_5V: JP5.1, Q4.3 (D), R6.2
SLEEPX: B2.A3, U8.4 (Q0)
SLEEPY: B2.A1, U8.6 (Q2)
SW_A: J6.3, U$1.O10
SW_B: J6.4, U$1.O11
SW_C: J7.3, U$1.O8
SW_D: J7.4, U$1.O9
SW_E: J8.3, U6.3 (A)
SW_EF_XOR: U1.4 (Y), U2.6 (C)
SW_E_BUF: U1.6 (C), U4.12 (PB0(ICP)), U6.4 (Y)
SW_F: J8.4, U5.3 (A)
SW_F_BUF: U1.1 (B), U1.3 (A), U4.13 (PB1(OC1A)), U5.4 (Y)
SW_OR_ENCODER: U2.4 (Y), U4.1 (PD3(INT1))
TXO: J11.3, U4.31 (PD1(TXD))
VCC_1: B2.5V, C11.2, IC2.8 (V+), J3.1, J5.12, J9.2, J11.2, J12.2, LED4.A, Q2.E, Q8.2 (G), R4.2, R6.1, R8.1, R10.1, R14.1, R20.2, U1.5 (VCC), U2.5 (VCC), U4.4 (VCC), U4.6 (VCC), U4.18 (AVCC), U5.5 (VCC), U6.5 (VCC), U7.5 (VCC), U8.16 (VCC)
VCC_2: B2.3.3V, J4.3, J5.2, J5.11, J6.5, J6.6, J7.5, J7.6, J8.5, J8.6, J10.6, J12.1, Q4.2 (G), Q5.2 (G), R11.1, R12.1, U$1.I1 (3.3V)
WAKE_LED: J10.1, U$1.O7
WAKE_SW: J10.3, U7.3 (A)
WAKE_SW_BUF: JP3.1, U2.3 (A), U4.14 (PB2(SS/OC1B)), U7.4 (Y)
XDIR: B2.D3 (*D3), U4.11 (PD7(AIN1))
XMS1: B2.D4, U8.14 (Q4)
XMS2: B2.D5 (*D5), U8.13 (Q5)
XSTEP: B2.D2, U4.10 (PD6(AIN0))
YDIR: B2.D7, U4.9 (PD5(T1))
YMS1: B2.D8, U8.12 (Q6)
YMS2: B2.D9 (*D9), U8.11 (Q7)
YSTEP: B2.D6 (*D6), U4.2 (PD4(XCK/T0))

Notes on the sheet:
PI Connection
LED Driver
IR Sensors
Switches
Radio
Hard reset on button hold (5s)
GPIO Expansions
Shift Register for motor settings NOTE: 5V
Power
Logic Level Converter
Extras
Extra I2C
Arduino
Headers to Motor Shield
SX1509 Headers for breakout board NOTE: 3.3V
Headers
Output to Raspberry Pi
Short JP2 to disable control of Pi Power from Arduino
Open JP3 to disable hard reset.
Combine the switch and Encoder Interupts

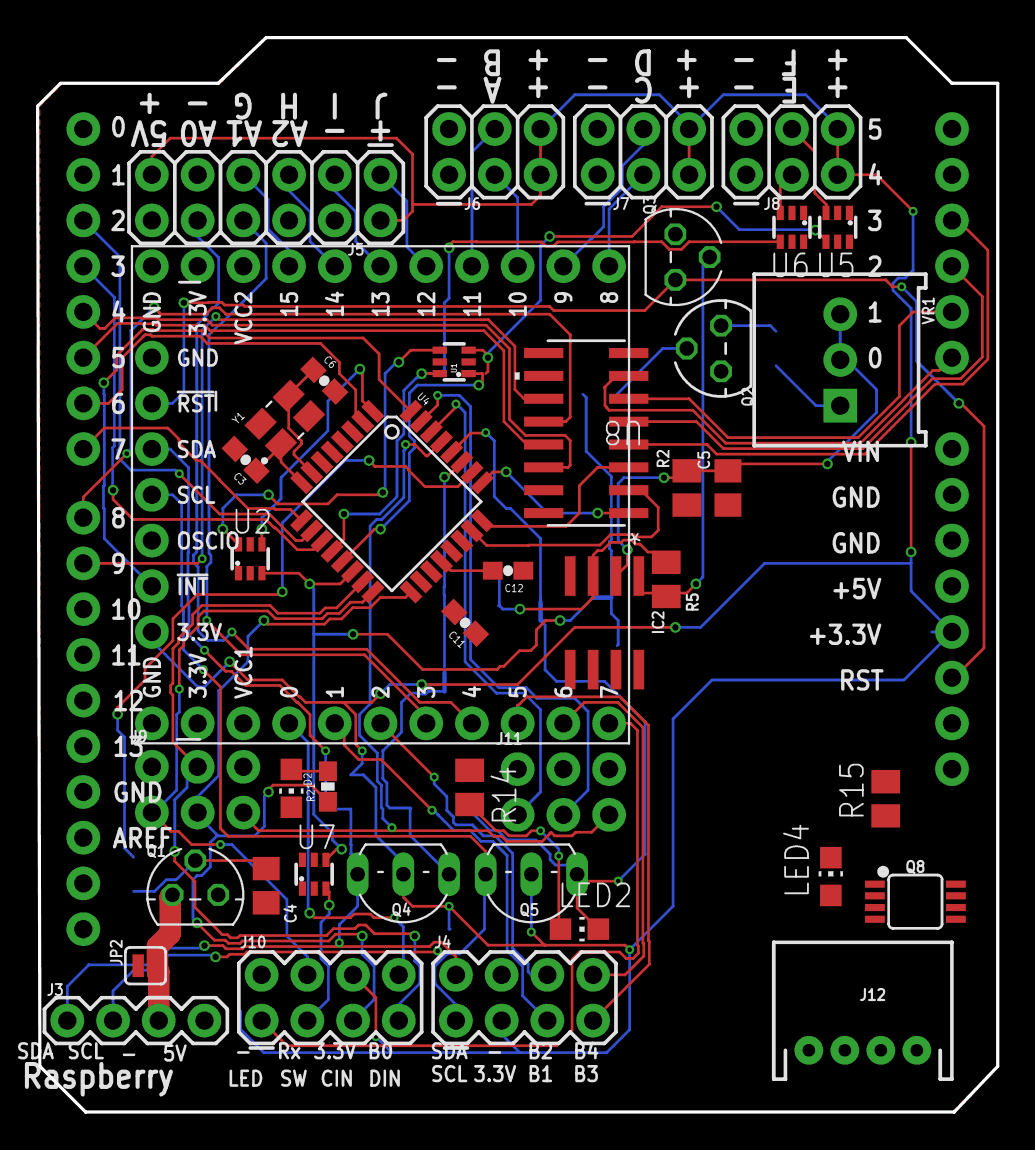
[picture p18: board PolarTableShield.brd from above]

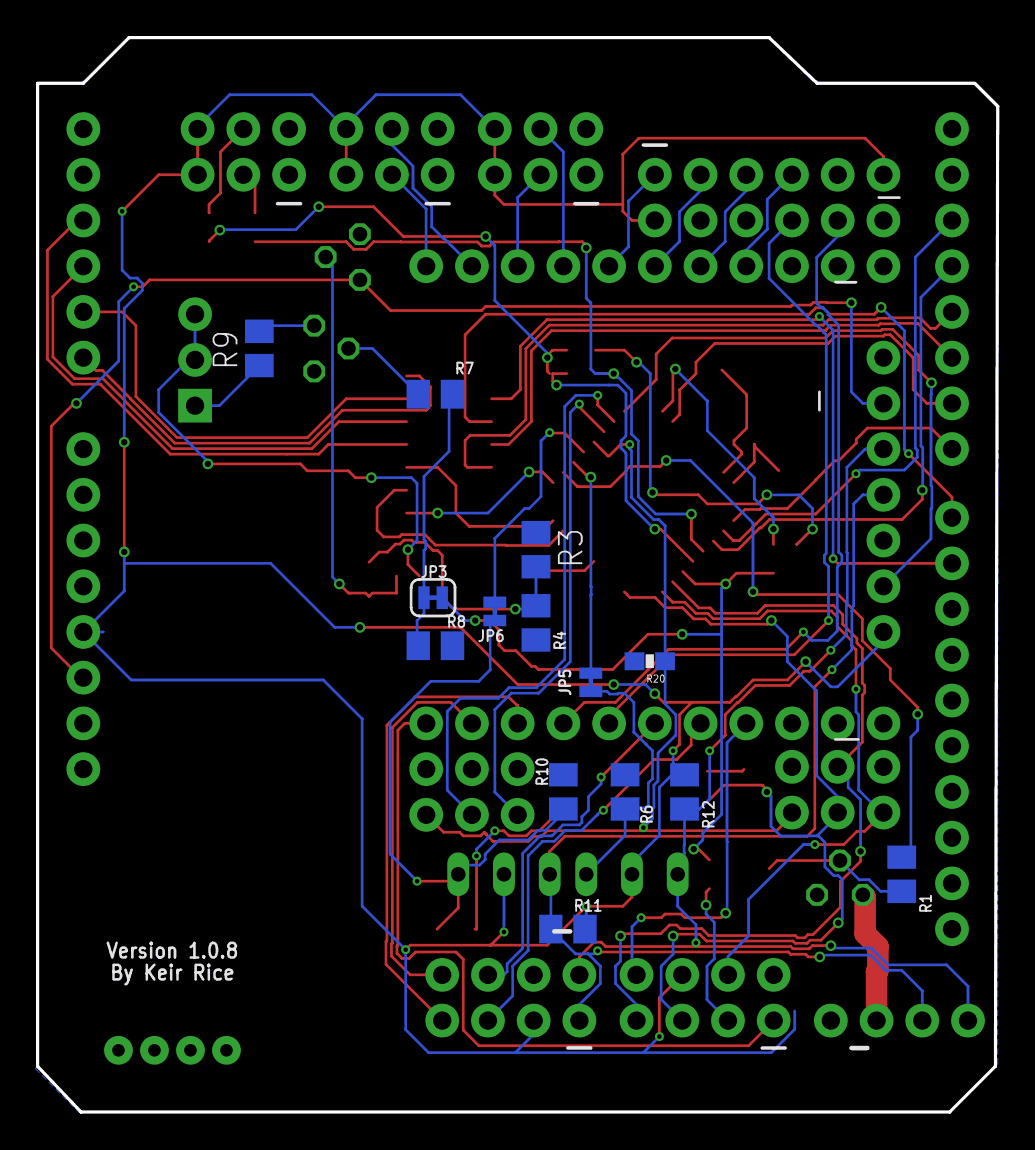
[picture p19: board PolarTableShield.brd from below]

Board: 2 copper layers, 53.3 x 59.7 mm, 58 parts (14 on the bottom side), 73 nets.

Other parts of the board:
U$3: TRI_LOGO_BOTTOM_5MM

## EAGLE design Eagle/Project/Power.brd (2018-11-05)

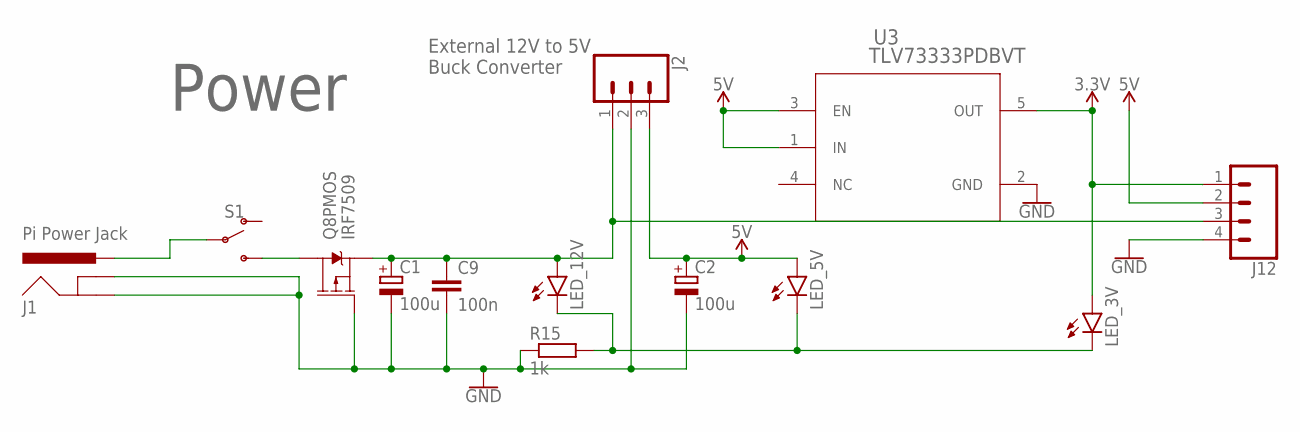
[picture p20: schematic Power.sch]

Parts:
C1, C2: 100u; E2-5
C9: 100n; C0805
J1: Pi Power Jack; POWER_JACK_PTH_BREAD
J2: Header - Right angled, female; 1X03
J12: CONN_04JST-PTH; JST-4-PTH
LED_3V, LED_5V, LED_12V: LEDCHIP-LED0805; CHIP-LED0805
Q8: IRF7509; MSOP8
R15: 1k; M0805
S1: SWITCH-SPDT-PTH-11.6X4.0MM; SWITCH_SPDT_PTH_11.6X4.0MM
U3: TLV73333PDBVT; DBV5

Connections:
12V_SUPPLY: C1.+, C9.1, J2.1, J12.3, LED_12V.A, Q8.3 (S)
GND: C1.-, C2.-, C9.2, J1.GND, J1.GNDBREAK, J2.2, J12.4, Q8.4 (G), R15.1, U3.2 (GND)
unnamed: Q8.5 (D), Q8.6 (D), S1.3 (S)
unnamed: J1.PWR, S1.2
unnamed: LED_3V.C, LED_5V.C, LED_12V.C, R15.2
VCC_1: C2.+, J2.3, J12.2, LED_5V.A, U3.1 (IN), U3.3 (EN)
VCC_2: J12.1, LED_3V.A, U3.5 (OUT)

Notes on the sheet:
Power
External 12V to 5V Buck Converter

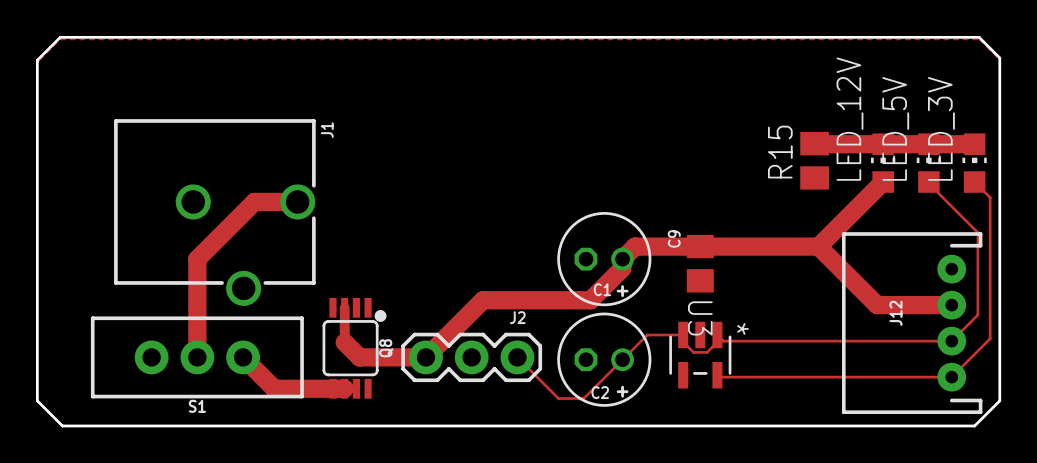
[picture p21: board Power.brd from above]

Board: 2 copper layers, 53.5 x 21.6 mm, 13 parts (0 on the bottom side), 7 nets.

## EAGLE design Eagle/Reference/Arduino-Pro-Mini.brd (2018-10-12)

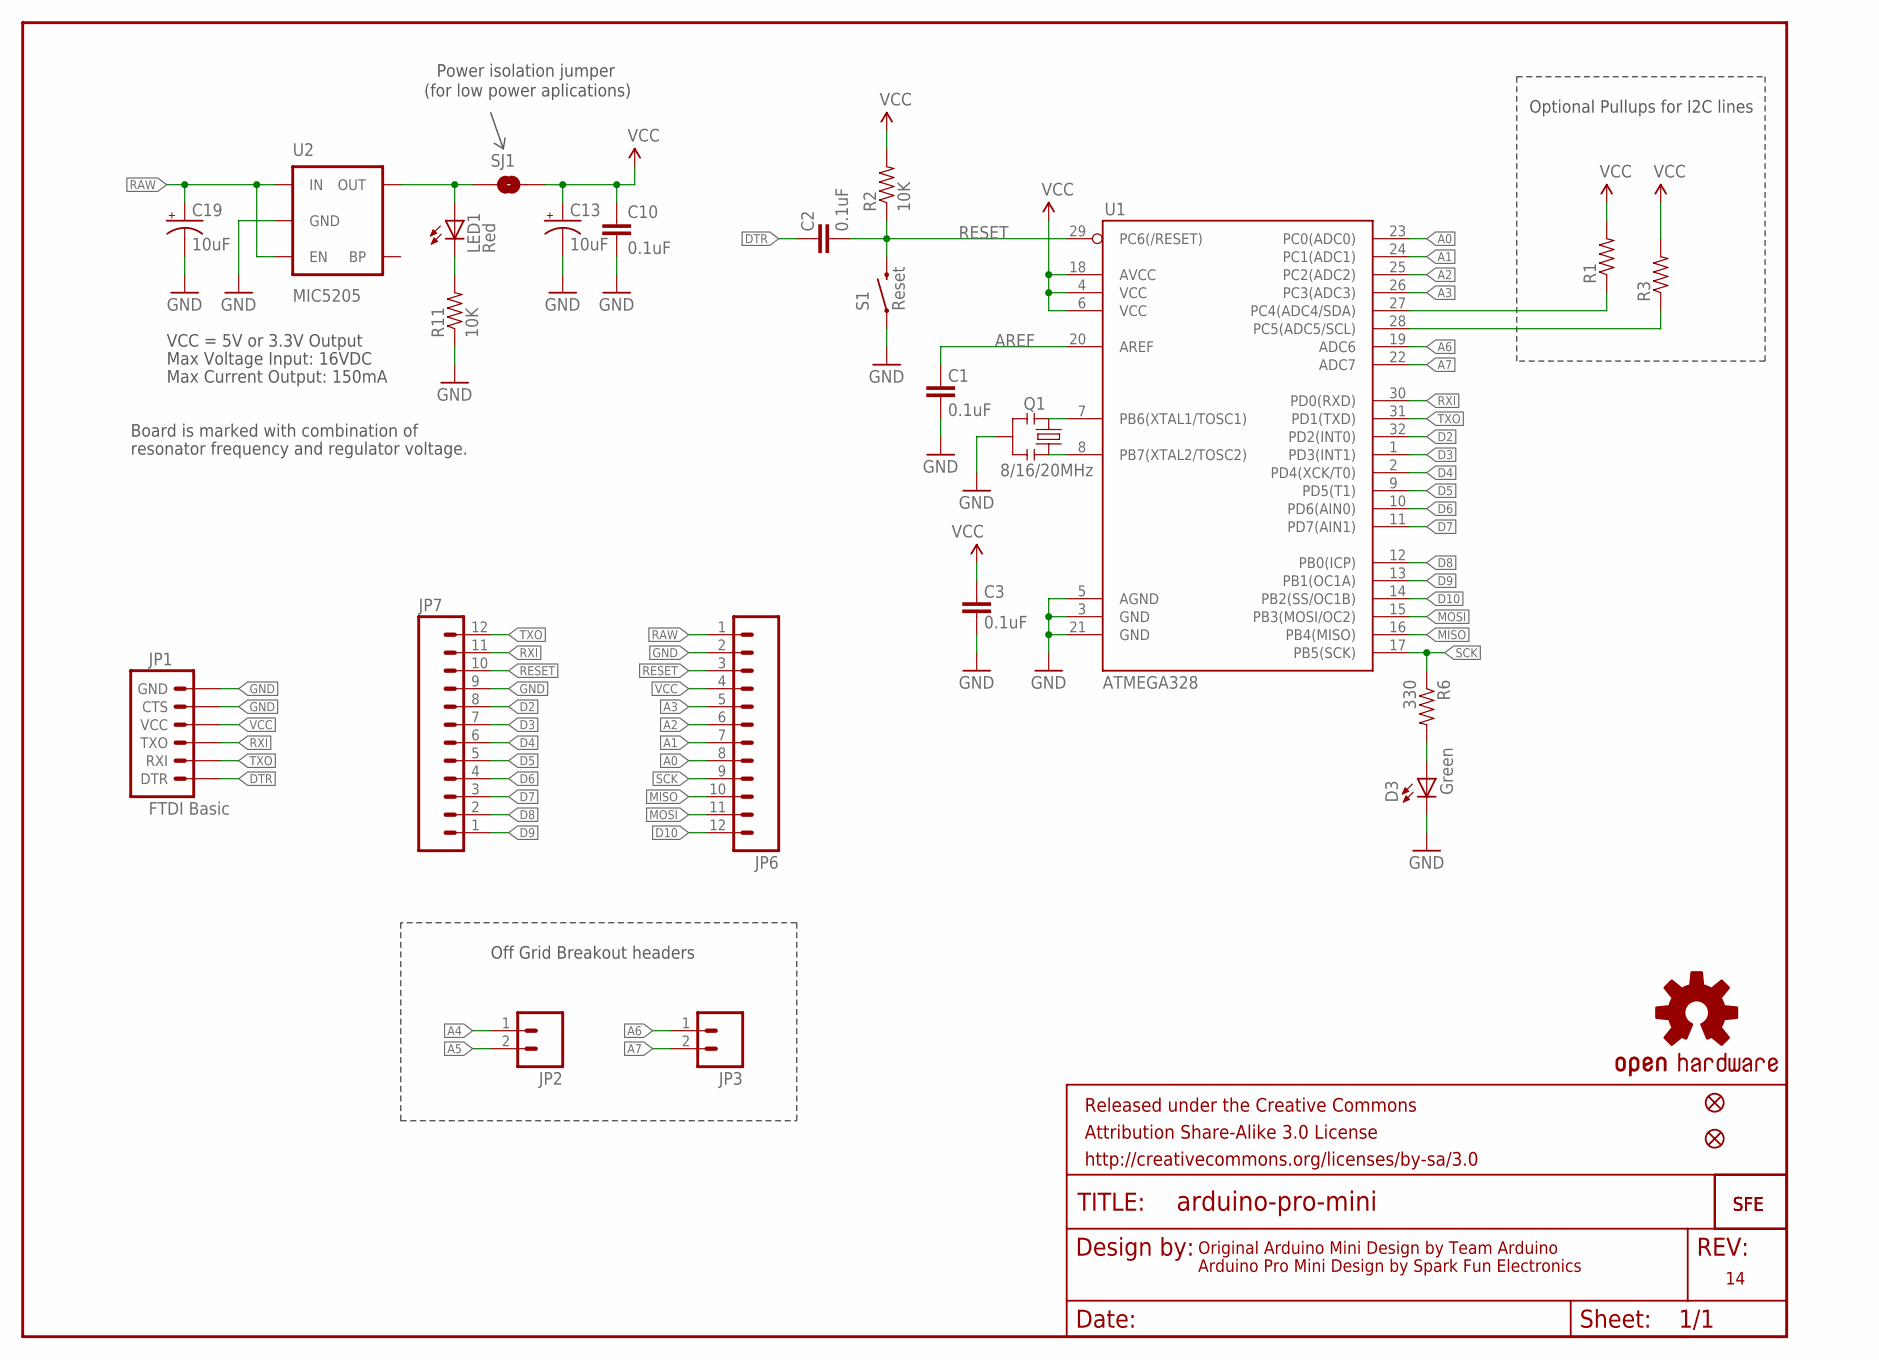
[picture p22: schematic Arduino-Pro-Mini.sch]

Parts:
C1, C2, C3, C10: 0.1uF; 0603-CAP
C13, C19: 10uF; EIA3216
D3: Green; 0603-LED-ALT1
FRAME1: FRAME-LETTER; CREATIVE_COMMONS
JP1: FTDI Basic; 1X06
JP2, JP3: M02PTH; 1X02
JP5, JP8: FIDUCIALUFIDUCIAL; MICRO-FIDUCIAL
JP6, JP7: M12PTH; 1X12
LED1: Red; 0603-LED-ALT1
Q1: 8/16/20MHz; RESONATOR-SMD-1:1
R1, R3: RESISTOR0603-RES; 0603-RES
R2, R11: 10K; 0603-RES
R6: 330; 0603-RES
S1: Reset; TACTILE-SWITCH-SMD-ALT01
SJ1: SOLDERJUMPERNC; SJ_2S
U1: ATMEGA328; TQFP32-08
U2: MIC5205; SOT23-5
U$1: LOGO-SFESK; SFE-LOGO-FLAME
U$3: OSHW-LOGOS; OSHW-LOGO-S
U$11: LOGO-SFENEW; SFE-NEW-WEBLOGO

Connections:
A0: JP6.8, U1.23 (PC0(ADC0))
A1: JP6.7, U1.24 (PC1(ADC1))
A2: JP6.6, U1.25 (PC2(ADC2))
A3: JP6.5, U1.26 (PC3(ADC3))
A4: JP2.1, R1.1, U1.27 (PC4(ADC4/SDA))
A5: JP2.2, R3.1, U1.28 (PC5(ADC5/SCL))
A6: JP3.1, U1.19 (ADC6)
A7: JP3.2, U1.22 (ADC7)
AREF: C1.2, U1.20 (AREF)
D2: JP7.8, U1.32 (PD2(INT0))
D3: JP7.7, U1.1 (PD3(INT1))
D4: JP7.6, U1.2 (PD4(XCK/T0))
D5: JP7.5, U1.9 (PD5(T1))
D6: JP7.4, U1.10 (PD6(AIN0))
D7: JP7.3, U1.11 (PD7(AIN1))
D8: JP7.2, U1.12 (PB0(ICP))
D9: JP7.1, U1.13 (PB1(OC1A))
D10: JP6.12, U1.14 (PB2(SS/OC1B))
DTR: C2.2, JP1.1 (DTR)
GND: C1.1, C3.1, C10.2, C13.C (-), C19.C (-), D3.C, JP1.5 (CTS), JP1.6 (GND), JP6.2, JP7.9, Q1.2, R11.1, S1.1, S1.2 (1), U1.3 (GND), U1.5 (AGND), U1.21 (GND), U2.2 (GND)
MISO: JP6.10, U1.16 (PB4(MISO))
MOSI: JP6.11, U1.15 (PB3(MOSI/OC2))
unnamed: Q1.3, U1.8 (PB7(XTAL2/TOSC2))
unnamed: Q1.1, U1.7 (PB6(XTAL1/TOSC1))
unnamed: LED1.A, SJ1.1, U2.5 (OUT)
unnamed: LED1.C, R11.2
unnamed: D3.A, R6.2
RAW: C19.A (+), JP6.1, U2.1 (IN), U2.3 (EN)
RESET: C2.1, JP6.3, JP7.10, R2.1, S1.3 (2), S1.4 (2), U1.29 (PC6(/RESET))
RXI: JP1.3 (TXO), JP7.11, U1.30 (PD0(RXD))
SCK: JP6.9, R6.1, U1.17 (PB5(SCK))
TXO: JP1.2 (RXI), JP7.12, U1.31 (PD1(TXD))
VCC: C3.2, C10.1, C13.A (+), JP1.4 (VCC), JP6.4, R1.2, R2.2, R3.2, SJ1.2, U1.4 (VCC), U1.6 (VCC), U1.18 (AVCC)

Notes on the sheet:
Original Arduino Mini Design by Team Arduino
Arduino Pro Mini Design by Spark Fun Electronics
Max Voltage Input: 16VDC
Max Current Output: 150mA
Board is marked with combination of
resonator frequency and regulator voltage.
VCC = 5V or 3.3V Output
Optional Pullups for I2C lines
Off Grid Breakout headers
Power isolation jumper
(for low power aplications)



Board: 2 copper layers, 17.8 x 33.0 mm, 29 parts (9 on the bottom side), 33 nets.

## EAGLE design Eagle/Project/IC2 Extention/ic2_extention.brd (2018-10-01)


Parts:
IC1: MCP23017SP; DIL28-3
J1: Input; 1X06_LOCK
J2: BankA; 1X08
J3: BankB; 1X08
R1: 10k; 0603
S1: DIP-04SMD; DIPSWITCH-04-SMD
SW1: Reset; BTN_CK_KSS

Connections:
A0: IC1.15 (A0), S1.6 (3B)
A1: IC1.16 (A1), S1.7 (2B)
A2: IC1.17 (A2), S1.8 (1B)
GND: IC1.10 (VSS), J1.1, SW1.P$1
unnamed: IC1.18 (!RESET), R1.1, SW1.P$2
unnamed: IC1.20 (INTA), J1.5
unnamed: IC1.19 (INTB), J1.4
unnamed: IC1.28 (GPA7), J2.1
unnamed: IC1.27 (GPA6), J2.2
unnamed: IC1.26 (GPA5), J2.3
unnamed: IC1.25 (GPA4), J2.4
unnamed: IC1.24 (GPA3), J2.5
unnamed: IC1.23 (GPA2), J2.6
unnamed: IC1.22 (GPA1), J2.7
unnamed: IC1.21 (GPA0), J2.8
unnamed: IC1.8 (GPB7), J3.1
unnamed: IC1.7 (GPB6), J3.2
unnamed: IC1.6 (GPB5), J3.3
unnamed: IC1.5 (GPB4), J3.4
unnamed: IC1.4 (GPB3), J3.5
unnamed: IC1.3 (GPB2), J3.6
unnamed: IC1.2 (GPB1), J3.7
unnamed: IC1.1 (GPB0), J3.8
unnamed: IC1.12 (SCL), J1.3
unnamed: IC1.13 (SDA), J1.2
VDD: IC1.9 (VDD), J1.6, R1.2, S1.1 (1A), S1.2 (2A), S1.3 (3A), S1.4 (4A)


Board: 2 copper layers, 35.2 x 50.8 mm, 7 parts (0 on the bottom side), 26 nets.

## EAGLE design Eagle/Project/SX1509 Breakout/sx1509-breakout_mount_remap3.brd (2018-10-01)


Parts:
B1: DownConnection; UNO_R3_SHIELD_NOLABELS
B2: UpConnection; UNO_R3_SHIELD_NOLABELS
C1, C2, C3, C4: 0.1uF; C0805
C5: 330uF; C0805
J1: Pi Power Jack; POWER_JACK_PTH_BREAD
J2: 12V to 5V; 1X03
J3: Pi Connection; 1X04
J4: CONN_03; 1X03
J5: IR Sensors; 1X06
J6: Switch A + B; 2X3
J7: Switch C + D; 2X3
J8: Switch E + F; 2X3
J9: CONN_03X2NO_SILK; 2X3-NS
J10: LED + Radio; 2X4
JP3: Enable Hold to Reset; SMT-JUMPER_2_NC_TRACE_SILK
JP5, JP6: CONN_11; 1X11
JP7: M07; 1X07
Q1: BC337; TO92
Q2: 2N3906; TO92D
Q3: BC547; TO92
R1: 100; R0805
R2: 22.1k; R0805
R3: 22k; R0805
R4: 16.2k; R0805
R5: 221k; R0805
R7, R8, R9: 1k; R0805
U1: OP-AMP; SO08
VR1: 10k; TRIMPOT-PTH-3386U

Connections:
3: JP5.7
3.3V: B1.3.3V, B2.3.3V, J4.1, J5.1, J6.5, J6.6, J7.5, J7.6, J8.5, J8.6, J10.8, JP5.2, JP6.2, JP7.7, Q2.E, R4.2, R8.1, R9.1, U1.8 (P$V+)
4: J5.3, JP5.8
5: J5.4, JP5.9
5V: B1.5V, B2.5V, C1.1, J2.3, J3.1
6: J5.5, JP5.10
7: J5.6, JP5.11
8: J6.3, JP6.11
9: J6.4, JP6.10
10: J7.3, JP6.9
10_TO_2: B1.D10 (*D10), B2.D2
11: J7.4, JP6.8
11_TO_3: B1.D11 (*D11), B2.D3 (*D3)
12: J8.3, JP6.7
12V: B1.VIN, B2.VIN, C2.2, C3.1, J1.PWR, J2.1
13: J8.4, JP6.6
14: J10.1, JP6.5
15: J9.4, JP6.4
15_PLUG: J4.2, J9.6
$N99: JP3.2, R7.2, R8.2
*D5: B1.D5 (*D5), B2.D5 (*D5)
*D6: B1.D6 (*D6), B2.D6 (*D6)
*D9: B1.D9 (*D9), B2.D9 (*D9)
A0: B1.A0, B2.A0
A1: B1.A1, B2.A1
A2: B1.A2, B2.A2
A3: B1.A3, B2.A3
AREF: B1.AREF, B2.AREF
COMP_OUT: Q3.2 (B), R5.1, U1.1 (OUT)
D4: B1.D4, B2.D4
D7: B1.D7, B2.D7
D8: B1.D8, B2.D8
D13: B1.D13, B2.D13
GND: B1.GND@0 (GND), B1.GND@1 (GND), B1.GND@2 (GND), B2.GND@0 (GND), B2.GND@1 (GND), B2.GND@2 (GND), C1.2, C2.1, C3.2, C4.2, C5.2, J1.GND, J1.GNDBREAK, J2.2, J4.3, J5.2, J6.1, J6.2, J7.1, J7.2, J8.1, J8.2, J9.5, J10.2, JP5.1, JP6.1, JP7.1, Q1.1 (E), R2.1, R3.1, U1.4 (P$V-)
IOREF: B1.IOREF, B2.IOREF
unnamed: Q2.B, R7.1
unnamed: C4.1, Q1.2 (B), R1.2
unnamed: Q3.3 (C), R9.2
unnamed: J9.2, R1.1
unnamed: R3.2, R4.1, R5.2, U1.2 (-IN)
unnamed: Q2.C, VR1.1 (CCW)
unnamed: C5.1, R2.2, U1.3 (+IN), VR1.2 (WIPER), VR1.3 (CW)
NINT: B1.D2, JP7.6
NRESET: B1.D12, JP7.2
OSCIO: JP7.5
PI_GROUND: J3.2, J9.3, Q1.3 (C)
RES: B1.RES, B2.RES, Q3.1 (E)
RX: B1.RX, B2.RX
RXDATA: J10.6, JP5.6
SCIN: J10.5, JP5.5
SCL: B1.A5, B1.SCL, B2.A5, B2.SCL, J3.3, JP7.4
SDA: B1.A4, B1.SDA, B2.A4, B2.SDA, J3.4, JP7.3
SDIN: J10.7, JP5.4
TX: B1.TX, B2.TX
VCC1: JP5.3
VCC2: JP6.3
WAKE_SW: B1.D3 (*D3), J10.3, JP3.1

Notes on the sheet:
LED Driver
IR Sensors
Switches
Radio
Long Press Detection (5s)
Jumpers for enabling pi power control. Connect 1-3 & 2-4 to have pin 15 high enable pi power. Connect 3-5 & 4-6 to have pi power always on and pin 15 to J4 connector.



Board: 2 copper layers, 55.9 x 59.7 mm, 35 parts (3 on the bottom side), 53 nets.

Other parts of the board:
U$2: TRI_LOGO_TOP_15MM

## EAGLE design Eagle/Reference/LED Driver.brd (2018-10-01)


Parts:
J1: CONN_04SCREW; SCREWTERMINAL-3.5MM-4
J2: CONN_023.5MM; SCREWTERMINAL-3.5MM-2
J3, J4: CONN_04JST-PTH; JST-4-PTH
Q1, Q2, Q3: 35A/25V/8.5mΩ; DPAK
U1: TXS0102; VFSOP-8

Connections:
unnamed: J2.2, Q1.4 (D), Q2.4 (D), Q3.4 (D)
unnamed: J1.2, Q1.3 (S)
unnamed: J1.3, Q2.3 (S)
unnamed: J1.4, Q3.3 (S)
unnamed: J1.1, J2.1
unnamed: J3.1, U1.P$3 (VCCA)
unnamed: J3.2, U1.P$5 (A1)
unnamed: J3.4, U1.P$7 (VCCB)

Board: 2 copper layers, 8 parts (0 on the bottom side), 8 nets, no tracks yet.

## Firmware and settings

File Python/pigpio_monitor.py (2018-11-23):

#!/usr/bin/env python
# -*- coding: utf-8 -*-

import time
import threading
import socket
import curses
import json
import Queue
from terminalsize import get_terminal_size

import locale
locale.setlocale(locale.LC_ALL, '')
code = locale.getpreferredencoding()


def encoder(string):
	"""Match the system encoding."""
	return string.encode(code)

UDP_PORT = 6000

# Simulation speed.
SIMULATION_SPEED = 0.1
SAMPLE_SPEED = SIMULATION_SPEED / 10.0

START_TIME = time.time()

NUDGE = 'nudge'
DETAIL = 'detail'

def millis():
	"""Milli seconds since script start."""
	return int((time.time() - START_TIME) * 1000)


# Server Side


class Signal(threading.Thread):
	"""Base class for different types of signal collectors."""

	__signals = list()

	def __init__(self, port, name):
		"""Init."""
		super(Signal, self).__init__()
		self.daemon = True

		self.name = name
		
		self.sock = socket.socket(socket.AF_INET, socket.SOCK_DGRAM)  # UDP
		self.sock.bind(('192.168.1.2', port))

		self.data = list()
		self.line = 0
		self.detail_selection_index = -1

		Signal.__signals.append(self)

	@classmethod
	def listen(cls):
		"""Start up all the signals."""
		for s in cls.__signals:
			s.start()

	def line_hint(self):
		"""The line number to display on."""
		# TODO: Decouple this...
		return self.line

	def run(self):
		"""Read incomming data and cach it for display."""
		while True:
			data, addr = self.sock.recvfrom(1024)  # buffer size is 1024 bytes
			incomming = json.loads(data.decode('utf-8'))
			incomming['arrived'] = millis()
			self.data.append(incomming)
	
	def present_timeline(self, skip=0, limit=-1):
		"""Return the most recent cached data upto the width."""
		return NotImplemented

	def present_table(self, skip=0, limit=-1):
		"""Return the most recent cached data upto the width."""
		return NotImplemented

	def pause(self, pause):
		"""Pause data capture?"""
		pass

	def length(self):
		"""Number of rows of data."""
		return len(self.data)

	def index_to_timestamp(self, index):
		"""Return the timestamp for the index."""
		return self.data[index]['timestamp']

	def timestamp_to_index(self, timestamp):
		"""Return the time stamp for the index."""
		closet_time = 99999999
		closet_index = -1
		last_time = closet_time

		for i, d in enumerate(self.data):
			test_time = abs(d['timestamp'] - timestamp)
			if test_time < closet_time:
				closet_time = test_time
				closet_index = i
			if test_time > last_time:
				break
			last_time = test_time
		return closet_index


class DataSignal(Signal):
	"""Data signals. Anything text based."""

	def __init__(self, name, port_offset, line):
		"""Init."""
		super(DataSignal, self).__init__(UDP_PORT + port_offset, name)
		self.line = line
		self.seperator = u''
		self.timeline_format_string = u'{}'
		self.timeline_format_width = 1

	def set_seperator(self, seperator):
		"""If the out put needs a seperator character set it here."""
		self.seperator = seperator
	
	def set_timeline_format_string(self, format_string, width):
		"""How are we presenting the data and how wide will if be."""
		self.timeline_format_string = format_string
		self.timeline_format_width = width

	def present_table(self, skip=0, limit=-1):
		"""Return the most recent cached data in table form."""
		skip = clamp(0, skip, len(self.data) - 1)

		if limit < 0:
			limit = len(self.data)
		limit = min(limit, len(self.data) - skip)

		lines = list()
		for data in self.data[skip:skip + limit]:
			if data['data'] == '':
				processed_data = (
					'{timestamp:>12d}ms '
					'{tag:<12s} ').format(
					timestamp=data['timestamp'],
					tag=data['tag'])

			else:
				processed_data = (
					'{timestamp:>12d}ms '
					'{tag:<12s} '
					'{data:#010b} '
					'      {data:#04X} '
					'       {data:>03d} '
					'{data:>10c} ').format(
					timestamp=data['timestamp'],
					tag=data['tag'],
					data=data['data'])

			lines.append(processed_data)

		return lines

	def present_timeline(self, skip=0, limit=-1):
		""""""
		skip = clamp(0, skip, self.length() - 1)
		
		data = list()
		counter = 0
		for d in self.data[skip:]:
			if d['data'] != '':
				data.append(self.timeline_format_string.format(d['data']))
				counter += 1
			if counter >= limit:
				break

		if limit < 0:
			limit = len(data) - 1
		limit = clamp(0, limit, len(data) - 1)

		label = u'{label:<10}'.format(
			label=self.name,
		)
		data_string = self.seperator.join(data)
		return label, data_string

	def width_to_limit(self, display_width):
		"""Return the max limit of data items that will fit in display_width."""
		label_width = 11
		timeline_width = display_width - label_width
		max_data_item_count = timeline_width // self.timeline_format_width
		return max_data_item_count


class PinSignal(Signal):
	"""Pin signals. Shows HIGH or LOW as well as transistions."""

	def __init__(self, name, pin):
		"""Init."""
		super(PinSignal, self).__init__(UDP_PORT + pin, name)
		self.line = self.pin = pin

	def present_timeline(self, skip=0, limit=-1):
		"""Return the most recent cached data upto the limit."""
		skip = clamp(0, skip, self.length() - 1)
		limit = clamp(0, limit, self.length() - 1 - skip)

		label = u'{name}({pin})'.format(name=self.name, pin=self.pin)

		data = [d['data'] for d in self.data[skip:skip + limit]]
		
		label = u'{label:<10}'.format(
			label=self.name,
		)
		data_string = u'{data}'.format(
			data=u''.join(data)
		)
		return label, data_string

	def width_to_limit(self, display_width):
		"""Return the max limit of data items that will fit in display_width."""
		label_width = 11
		timeline_width = display_width - label_width
		data_format_width = 1
		max_data_item_count = timeline_width // data_format_width
		return max_data_item_count


class Window(object):
	"""Curses Window."""

	status_window = None

	def __init__(self, stdscr):
		"""Init."""
		self.stdscr = stdscr

		self.quit = False
		self.paused = False
		
		self.selection_mode = None
		self.timeline_selection_index = -1
		self.timeline_selection_timestamp = -1
		self.detail_selection_index = -1
		self.detail_selection_timestamp = -1

		self.detail_selection_timestamp = -1

		self.detail_length = 0
		self.detail_data_window = None
		self.timeline_data_window = dict()

		self.sections = list()

		self.header_layout = None
		self.timeline_layout = None
		self.details_layout = None
		self.status_layout = None

		self.header_win = None
		self.timeline_win = None
		self.details_win = None
		self.status_win = None

		self.header_win_border = (0, 0, 0, 0, 0, 0, curses.ACS_LTEE, curses.ACS_RTEE)
		self.timeline_win_border = (0, 0, ' ', 0, curses.ACS_VLINE, curses.ACS_VLINE, curses.ACS_VLINE, curses.ACS_VLINE)
		self.details_win_border = (0, 0, ' ', 0, curses.ACS_VLINE, curses.ACS_VLINE, 0, 0)
		self.status_win_border = (0, 0, 0, 0, 0, 0, 0, 0)
		
		self.windows = list()

		self.height, self.width = get_terminal_size()

		self.create()
		self.content()
		self.border()
		self.refresh()

	def create(self):
		"""Create the windows."""
		self.layout()
		self.header_win = curses.newwin(*self.header_layout)
		self.windows.append(self.header_win)
		self.timeline_win = curses.newwin(*self.timeline_layout)
		self.windows.append(self.timeline_win)
		self.details_win = curses.newwin(*self.details_layout)
		self.windows.append(self.details_win)
		self.status_win = curses.newwin(*self.status_layout)
		self.windows.append(self.status_win)
		Window.status_window = self.status_win

	def layout(self):
		"""Calculate the sizes and locations of the windows."""
		self.width, self.height = get_terminal_size()
		
		header_height = 3
		timeline_height = 8
		status_height = 4
		details_height = self.height - header_height - timeline_height - status_height
		
		header_start = 0
		timeline_start = header_height
		details_start = timeline_start + timeline_height
		status_start = details_start + details_height

		self.header_layout = (header_height, self.width, header_start, 0)
		self.timeline_layout = (timeline_height, self.width, timeline_start, 0)
		self.details_layout = (details_height, self.width, details_start, 0)
		self.status_layout = (status_height, self.width, status_start, 0)

	def resize(self):
		"""Re-apply the layouts to the windows."""
		self.layout()

		for window in self.windows:
			window.erase()

		self.header_win.resize(self.header_layout[0], self.header_layout[1])
		self.timeline_win.resize(self.timeline_layout[0], self.timeline_layout[1])
		self.details_win.resize(self.details_layout[0], self.details_layout[1])
		self.status_win.resize(self.status_layout[0], self.status_layout[1])

		self.header_win.mvwin(self.header_layout[2], self.header_layout[3])
		self.timeline_win.mvwin(self.timeline_layout[2], self.timeline_layout[3])
		self.details_win.mvwin(self.details_layout[2], self.details_layout[3])
		self.status_win.mvwin(self.status_layout[2], self.status_layout[3])

		self.content()
		self.border()
		self.refresh()

	def border(self):
		"""Add the borders."""
		self.header_win.border(*self.header_win_border)
		self.timeline_win.border(*self.timeline_win_border)
		self.details_win.border(*self.details_win_border)
		self.status_win.border(*self.status_win_border)

	def refresh(self):
		for window in self.windows:
			window.refresh()

	def content(self):
		self.header_content()
		self.details_content()
		self.status_content()
	
	def header_content(self):
		self.header_win.addstr(1, 1, 'I2C Watcher', curses.color_pair(2) | curses.A_BOLD)
		address = ip_address()
		self.header_win.addstr(1, self.width - 1 - len(address), address)
		
	def details_content(self):
		details_header = '{:>14} {:>12s} {:>10} {:>10} {:>10} {:>10}'.format(
			'Timestamp',
			'Tag',
			'Binary',
			'Hex',
			'Decimal',
			'ASCII'
		)
		self.details_win.addstr(0, 1, encoder(clip(details_header, self.width - 2)), curses.color_pair(2) | curses.A_BOLD)
	
	def status_content(self):
		help_text = u'Commands: (P)ause, (←) Scrub Left, (→) Scrub Right, (Q)uit'
		self.status_win.addstr(1, 1, encoder(clip(help_text, self.width - 2)))

	def timeline(self, timeline_signals):
		"""Pump the timeline."""
		self.timeline_win.erase()
		content_width = self.width - 2
		content_center = content_width // 2
		label_size = 11

		for i, s in enumerate(timeline_signals):

			limit = s.width_to_limit(content_width)

			if self.paused:
				offset, limit = self.timeline_data_window[i]
				
				self.timeline_selection_index = offset + content_center - label_size
				self.timeline_selection_timestamp = timeline_signals[i].index_to_timestamp(self.timeline_selection_index)

				if self.selection_mode == NUDGE:
					pass
				elif self.selection_mode == DETAIL:
					offset = s.timestamp_to_index(self.detail_selection_timestamp) - content_center + label_size
					self.timeline_data_window[i] = offset, limit
				else:
					pass
				
			else:
				limit = min(limit, s.length())
				offset = max(0, s.length() - limit)
				self.timeline_data_window[i] = offset, limit

			max_padding = (content_center - label_size)
			if (offset + max_padding) >= 0:
				pass
			else:
				offset = -max_padding

			label, stream = s.present_timeline(offset, limit)
			
			# Handle when the data samples are not exactly 1 char wide and we need to clip to prevent overflow.
			padding = content_width - len(label) - 1 - len(stream)
			if padding > 0:
				stream = (u' ' * padding) + stream

			self.timeline_win.addstr(s.line_hint(), 1, encoder(label + ' ' + stream))

		# Reset the selection timestamp so it doesn't override the nudge each frame.
		self.detail_selection_timestamp = -1

		if self.paused:
			height, width = self.timeline_win.getmaxyx()
			center = width // 2
			for line in range(1, height - 1):
				self.timeline_win.chgat(line, center, 1, curses.A_REVERSE)
			try:
				offset, limit = self.timeline_data_window[0]
				timestamp = timeline_signals[0].index_to_timestamp(offset)
				self.timeline_win.addstr(6, center + 1, encoder('{:d}ms'.format(timestamp)))
			except IndexError:
				pass

		self.timeline_win.border(*self.timeline_win_border)
		self.details_content()
		self.timeline_win.refresh()

	def details(self, detail_signal):
		self.timeline_win.erase()

		if self.detail_selection_index != -1:
			self.detail_selection_timestamp = detail_signal.index_to_timestamp(self.detail_selection_index)

		self.detail_length = detail_signal.length()

		if self.paused:
			offset, limit = self.detail_data_window

			if self.selection_mode == NUDGE:
				self.detail_selection_index = detail_signal.timestamp_to_index(self.timeline_selection_timestamp)

			elif self.selection_mode == DETAIL:
				pass
			else:
				pass

		else:
			hy, hx = self.details_win.getmaxyx()
			hy -= 3  # Heading + borders
			offset = max(0, detail_signal.length() - hy)
			limit = min(hy, detail_signal.length())
			self.detail_data_window = offset, limit

		table = detail_signal.present_table(offset, limit)
		
		row_number = offset
		for line_number, row_text in enumerate(table):
			self.details_win.move(line_number + 2, 1)
			self.details_win.clrtoeol()

			if self.detail_selection_index >= 0 and row_number == self.detail_selection_index:
				self.details_win.addstr(line_number + 2, 1, row_text, curses.color_pair(1) | curses.A_BOLD)
			else:
				self.details_win.addstr(line_number + 2, 1, row_text, curses.color_pair(2))

			row_number += 1
			
		self.details_win.border(*self.details_win_border)
		self.details_content()
		self.details_win.refresh()

	def update_selection(self, up=True):
		"""Update the selections."""
		# Move the selection in details.
		if not self.paused:
			return

		self.selection_mode = DETAIL
		offset, limit = self.detail_data_window

		if up:
			self.detail_selection_index -= 1
			if self.detail_selection_index > (offset + limit):
				self.detail_selection_index = (offset + limit)
		else:
			self.detail_selection_index += 1
			if self.detail_selection_index < offset:
				self.detail_selection_index = offset
		self.detail_selection_index = clamp(0, self.detail_selection_index, self.detail_length - 1)

		# Bump scroll the details list.
		if self.detail_selection_index >= (offset + limit):
			offset += 1
			self.detail_data_window = (offset, limit)
		elif self.detail_selection_index < offset:
			offset -= 1
			self.detail_data_window = (offset, limit)

	def nudge_timeline(self, left=True, boost=False):
		# TODO: Make a nice acceleration based on hold time.
		if not self.paused:
			return
		self.selection_mode = NUDGE
		move = -1 if left else 1
		if boost:
			move *= 10
		for row, (offset, limit) in self.timeline_data_window.iteritems():
			self.timeline_data_window[row] = (max(0, offset + move), limit)

	def process_input(self):
		"""Process key presses."""
		# self.status_win.nodelay(False)
		# curses.halfdelay(10)

		KEY_UP = 0x41
		KEY_DOWN = 0x42
		KEY_RIGHT = 0x43
		KEY_LEFT = 0x44
		KEY_ESC = 27

		while not self.quit:
			try:
				c = self.status_win.getch()
			except curses.ERR:
				continue

			if c == KEY_ESC:  # Esc or Alt
				self.status_win.nodelay(True)
				n = self.status_win.getch()
				if n == -1:
					self.quit = True  # Escape
				self.status_win.nodelay(False)
				# self.status_win.halfdelay(10)

			elif c == KEY_UP:
				self.update_selection(True)
			elif c == KEY_DOWN:
				self.update_selection(False)
			elif c == KEY_LEFT:
				self.nudge_timeline(True)
			elif c == KEY_RIGHT:
				self.nudge_timeline(False)
			# elif c == KEY_SLEFT:
			# 	self.nudge_timeline(True, True)
			# elif c == KEY_SRIGHT:
			# 	self.nudge_timeline(False, True)
			elif c == curses.KEY_RESIZE:
				self.resize()
			elif c == curses.KEY_HOME:
				return
			elif c in (ord('q'), ord('Q')):
				self.quit = True
			elif c in (ord('p'), ord('P')):
				self.paused = not self.paused
				if not self.paused:
					self.selection_mode = None
				type(self).set_status(u'pause = {}'.format(self.paused))

	@classmethod
	def set_status(cls, *args):
		"""Put text in the status line."""
		width, _ = get_terminal_size()
		text = u' '.join([unicode(a) for a in args])
		text = clip(text, width - 2)
		
		cls.status_window.move(2, 1)
		cls.status_window.clrtoeol()
		cls.status_window.addstr(2, 1, encoder(text))
		cls.status_window.border()
		cls.status_window.refresh()


def clip(text, width):
	"""Clip text to a fixed width."""
	return text[:min(len(text), width)]


def clamp(minimum, value, maximum):
	"""Clamp the value between the min and max."""
	return min(max(minimum, value), maximum)

def ip_address():
	"""Return out IP address."""
	local_ips = [ip for ip in socket.gethostbyname_ex(socket.gethostname())[2] if not ip.startswith("127.")]
	socket_message = [socket.socket(socket.AF_INET, socket.SOCK_DGRAM)]
	remote_ips = [[(s.connect(("8.8.8.8", 53)), s.getsockname()[0], s.close()) for s in socket_message][0][1]]
	return ((local_ips or remote_ips) + ["no IP found"])[0]


def main():
	ur"""Setup a window to work in.

	********************************************************************************
	I2C Watcher
	********************************************************************************



	SDA(2) /‾‾‾‾‾‾‾‾‾‾‾‾‾‾‾‾‾‾\____________________________________________________________
	SCL(3) _____/‾‾‾‾‾‾‾‾\________/‾‾‾‾‾‾‾‾‾\________/‾‾‾‾‾‾‾‾\________/‾‾‾‾‾‾‾‾‾\________/
	BIT                           0                  0                  0                 0

	DATA 14

	"""
	stdscr = curses.initscr()
	curses.start_color()
	curses.init_pair(1, curses.COLOR_BLUE, curses.COLOR_BLACK)
	curses.init_pair(2, curses.COLOR_WHITE, curses.COLOR_BLACK)
	
	curses.noecho()
	curses.cbreak()
	curses.curs_set(False)
	
	try:
		w = Window(stdscr)

		data_signal = DataSignal('DATA', 101, 6)  # The data in hex
		timeline_signals = [
			PinSignal('SDA', 2),  # SDA signal pin
			PinSignal('SCL', 3),  # SCL signal pin
			DataSignal('BIT   ', 100, 4),  # The bits as they get read
		]

		# Start listening
		Signal.listen()

		threading.Thread()
		t = threading.Thread(target=w.process_input)
		t.start()

		while not w.quit:
			w.timeline(timeline_signals)
			w.details(data_signal)
			# w.process_input()
			pass

	finally:
		stdscr.keypad(0)
		curses.curs_set(True)
		curses.nocbreak()
		curses.echo()
		curses.endwin()

if __name__ == '__main__':
	main()

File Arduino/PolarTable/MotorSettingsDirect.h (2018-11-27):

/*************************************************************
  Motor control
*************************************************************/
#pragma once

#ifdef DISABLE_MOTORS

void motor_settings_setup() {}

#else

/*************************************************************
  Variables
*************************************************************/

static const byte FULL_STEP = 0b00;
static const byte HALF_STEP = 0b10;
static const byte QUARTER_STEP = 0b01;
static const byte EIGHTH_STEP = 0b11;

/*************************************************************
  Functions
*************************************************************/

void motor_sleep(boolean do_sleep)
{
  digitalWrite(PIN_MOTOR_SLEEPX, do_sleep ? 0 : 1);
  digitalWrite(PIN_MOTOR_SLEEPY, do_sleep ? 0 : 1);
}

void motor_enable(boolean enable)
{
  digitalWrite(PIN_MOTOR_ENABLEX, enable ? 0 : 1);
  digitalWrite(PIN_MOTOR_ENABLEY, enable ? 0 : 1);
}

void motor_wake_and_enable() {
  /* Optimised version below
 
    // SLEEP active on low
    motor_sleep(false);
    // ENABLE active on low
    motor_enable(true);
  */

  PORTA = (PORTA & 0b11110000) | 0b00000101
}

/*************************************************************
  Setup and Main loop
*************************************************************/

void motor_settings_setup() {
  /* We use a shift register for the motor settings. */
  // Set pins to output because they are addressed in the main loop
  pinMode(PIN_MOTOR_SLEEPX, OUTPUT);
  pinMode(PIN_MOTOR_ENABLEX, OUTPUT);
  pinMode(PIN_MOTOR_SLEEPY, OUTPUT);
  pinMode(PIN_MOTOR_ENABLEY, OUTPUT);
  pinMode(PIN_MOTOR_XMS1, OUTPUT);
  pinMode(PIN_MOTOR_XMS2, OUTPUT);
  pinMode(PIN_MOTOR_YMS1, OUTPUT);
  pinMode(PIN_MOTOR_YMS2, OUTPUT); 

  // Wake, enable, and set full steps
  PORTA = 0b00000101;
}

#endif // DISABLE_MOTORS

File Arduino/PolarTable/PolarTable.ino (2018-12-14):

#include "Debug.h"

#define MEGA

typedef unsigned int uint;

#define THETA_MAX_TRAVEL 1000
#define RADIUS_MAX_TRAVEL 1000

#include "PinsMega.h"

#include <kPin.h>

#include <kEvent.h>
#include "EventTypes.h"
EventManager evtManager;
#include <Fsm.h>

typedef struct FsmEventDriver : public EventTask
{
  Fsm *fsm;
  FsmEventDriver();
  FsmEventDriver(Fsm *statemachine) : fsm(statemachine) {}

  using EventTask::execute;
  
  void execute(Event *evt)
  {
    // DEBUG_PRINT_VAR("FsmEventDriver ", *(EventID*)evt->extra);
    fsm->trigger(*(EventID*)evt->extra);
  }
} FsmEventDriver;

#define EI_NOTEXTERNAL
#include <EnableInterrupt.h>
#include <kEncoder.h>
kEncoder::AbsoluteEncoder abs_encoder;
kEncoder::RelativeEncoder rel_encoder;


void abs_encoder_isr(){
  abs_encoder.interputHandler();
}
void rel_encoder_isr(){
  rel_encoder.interputHandler();
}

#include "ProjectEvents.h"
#include "Helpers.h"

#include "ESP.h"
#include "Button.h"
#include "Calibration.h"
#include "Lighting.h"
#include "Motors.h"
#include "Commands.h"


void setup()
{
  if (DEBUG) {
    Serial.begin(115200);
  }
  DEBUG_PRINTLN("Setup serial.");
  DEBUG_WHERE();

  esp_setup();
  button_setup();
  button_led_setup();
  lighting_setup();
  motor_setup();
  calibration_setup();
  command_setup();

  // Encode setup.
#ifndef DISABLE_ENCODER_ABSOLUTE
  kPin::Group::Port *asb_port = new kPin::Group::Port(kPin::PORT_K, 0b00001111);
  abs_encoder.setup((*asb_port), &abs_encoder_isr);
#endif // DISABLE_ENCODER_ABSOLUTE
#ifndef DISABLE_ENCODER_RELATIVE
  kPin::Group::Port *rel_port = new kPin::Group::Port(kPin::PORT_K, 0b00110000);
  rel_encoder.setup((*rel_port), &rel_encoder_isr);
#endif // DISABLE_ENCODER_RELATIVE
  
  // testing_setup();
  DEBUG_WHERE();
}

void loop()
{
//  esp_loop();
//  button_loop();
//  button_led_loop();
//  lighting_loop();
//  motor_loop();
//  calibration_loop();
//  command_loop();
}
//void setup(){}
//void loop(){}

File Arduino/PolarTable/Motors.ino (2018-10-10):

/*************************************************************
Motor control
*************************************************************/

#include <AccelStepper.h>
#include <MultiStepper.h>

// Define some steppers and the pins the will use
AccelStepper theta_stepper(AccelStepper::DRIVER, PIN_MOTOR_YSTEP, PIN_MOTOR_YDIR);
AccelStepper radius_stepper(AccelStepper::DRIVER, PIN_MOTOR_XSTEP, PIN_MOTOR_XDIR);
MultiStepper stepper = MultiStepper();

/*************************************************************
Variables
*************************************************************/

// static const char sleepXMask = 1 << PIN_MOTOR_SLEEPX;
// static const char enXMask = 1 << PIN_MOTOR_ENABLEX;
// static const char sleepYMask = 1 << PIN_MOTOR_SLEEPY;
// static const char enYMask = 1 << PIN_MOTOR_ENABLEY;
// static const char yMSMask = 3 << PIN_MOTOR_YMS1; // 3 == b11
// static const char xMSMask = 3 << PIN_MOTOR_XMS1; // 3 == b11

static const char FULL_STEP = 0; // b00
static const char HALF_STEP = 2; // b10
static const char QUARTER_STEP = 1; // b01
static const char EIGHTH_STEP = 3; // b11


/*************************************************************
State
*************************************************************/

const char DATA_STATE_IDLE = 0;
const char DATA_STATE_CHANGED = 1;
const char DATA_STATE_SENDING = 2;
char DATA_STATE = 0;

unsigned long dataSendTimer = 0;
unsigned char motor_settings = 0;
bool motor_settings_changed = true;

static const int MOTOR_STATE_ERROR = 0;
static const int MOTOR_STATE_STOPPING = 6;
static const int MOTOR_STATE_STOPPED = 1;
static const int MOTOR_STATE_MOVING = 2;
static const int MOTOR_STATE_IDLE = 3;
static const int MOTOR_STATE_SLEEP = 4;
static const int MOTOR_STATE_WAKE = 5;

static const int MOTOR_STATE_TO_STOPPING = 16;
static const int MOTOR_STATE_TO_STOPPED = 11;
static const int MOTOR_STATE_TO_MOVING = 12;
static const int MOTOR_STATE_TO_IDLE = 13;
static const int MOTOR_STATE_TO_SLEEP = 14;
static const int MOTOR_STATE_TO_WAKE = 15;

/*═════════╦═══════╦═════════╦══════════╦════════╦══════╦═══════╦══════╗
║                ║ error      ║ stopped       ║ stopping        ║ moving       ║ idle     ║ sleep      ║ wake     ║
╠═════════╬═══════╬═════════╬══════════╬════════╬══════╬═══════╬══════╣
║ error    ║       ║         ║          ║        ║      ║       ║      ║
║ stopped  ║       ║         ║        1 ║        ║    1 ║       ║    1 ║
║ stopping ║       ║         ║          ║      1 ║      ║       ║      ║
║ moving   ║       ║       1 ║          ║        ║      ║       ║      ║
║ idle     ║       ║       1 ║          ║        ║      ║       ║      ║
║ sleep    ║       ║         ║          ║        ║    1 ║       ║      ║
║ wake     ║       ║         ║          ║        ║      ║     1 ║      ║
╚══════════╩═══════╩═════════╩══════════╩════════╩══════╩═══════╩═════*/

int MOTOR_STATE = 3;

unsigned int stoppedTimer = 0;
unsigned int idleTimer = 0;

long absolute_position_in_steps[2] = {0, 0};
bool new_position = false;


/*************************************************************
Functions
*************************************************************/

void get_motor_position(motor motors[]){
  motors[0].steps = theta_stepper.currentPosition();
  motors[1].steps = radius_stepper.currentPosition();
}

void set_theta_motor_position(motor motor){
  theta_stepper.moveTo(motor.steps);
}

void set_delta_motor_position(motor motor){
  radius_stepper.moveTo(motor.steps);
}

void set_position_in_motor_steps(long theta, long delta)
{
  absolute_position_in_steps[0] = theta; 
  absolute_position_in_steps[1] = delta;
  new_position = true;
}

void send_state() {
  // turn off the output so the pins don't light up
  // while you're shifting bits:
  digitalWrite(PIN_SHIFT_LATCH, LOW);

  // shift the bits out:
  shiftOut(PIN_SHIFT_DATA, PIN_SHIFT_CLOCK, MSBFIRST, motor_settings);

  // turn on the output so the LEDs can light up:
  digitalWrite(PIN_SHIFT_LATCH, HIGH);
  
  dataSendTimer = millis() + 1;
  motor_settings_changed = false;
}


/*************************************************************
Setup and Main loop
*************************************************************/

void motor_setup() {
  
  theta_stepper.setMaxSpeed(200.0);
  theta_stepper.setMinPulseWidth(20); // Driver supports 1us
  // theta_stepper.setAcceleration(200.0);
  
  radius_stepper.setMaxSpeed(100.0);
  radius_stepper.setMinPulseWidth(20); // Driver supports 1us
  // radius_stepper.setAcceleration(100.0);
  
  stepper.addStepper(theta_stepper);
  stepper.addStepper(radius_stepper);

  /* We use a shift register for the motor settings. */
  // Set pins to output because they are addressed in the main loop
  pinMode(PIN_SHIFT_LATCH, OUTPUT);
  pinMode(PIN_SHIFT_DATA, OUTPUT);  
  pinMode(PIN_SHIFT_CLOCK, OUTPUT);
  
  // Full steps
  bitsWrite(motor_settings, PIN_MOTOR_XMS1, FULL_STEP, 2);
  bitsWrite(motor_settings, PIN_MOTOR_YMS1, FULL_STEP, 2);
  
  // Enable (Sleep is active low)
  bitWrite(motor_settings, PIN_MOTOR_ENABLEX, 1);
  bitWrite(motor_settings, PIN_MOTOR_ENABLEY, 1);
  
  // Turn off sleep (Sleep is active low)
  bitWrite(motor_settings, PIN_MOTOR_SLEEPX, 1);
  bitWrite(motor_settings, PIN_MOTOR_SLEEPY, 1);
  
  send_state();
}
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

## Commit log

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2018-10-01 Hardware designs
    [Assembly.fcstd, Belt.FCStd, Belt2.FCStd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]
2018-10-01 Reference hardware designs.
    [LED Strip driver.brd, LED Strip driver.sch, arduino_2009.brd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]
2018-10-01 Eagle designs for electronic components.
    [LED Driver.brd, LED Driver.sch, ic2_extention.brd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]
2018-10-01 Python simulation code.
    [heart.dwg]
2018-10-02 Outputs from eagle
    [Table Electronics BOM 2.0 - Sheet6.tsv]
2018-10-02 Images and exports
    [combined.dxf, copper.dwg, copper_pour.dxf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]
2018-10-02 Sorting out file locations.
    [Assembly.fcstd, Belt.FCStd, Belt2.FCStd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]
2018-10-02 Snapshot of the fusion 360 files.
    [Table.f3z]
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2018-10-02 Upgrade Eagle + Organised files
    [LED Driver.brd, LED Driver.sch, ic2_extention.brd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]
2018-10-02 Renamed the head of the eagle files
    [PolarTableShield.brd, PolarTableShield.csv, PolarTableShield.sch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]
2018-10-03 Added a custom SX1509 footprint and device.
    Added a custom SX1509 footprint and device so I can do proper pin swaps and manage the silks a bit easier.
2018-10-03 Expanded board
    Remove my self imposed footprint restriction.
    Add circuit for analog to 1bit digital signal for the IR sensors.
    Added the new SX1509 custom device.
    [PolarTableShield.brd, PolarTableShield.sch]
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2018-10-09 Back to normal shield size
    Removed the sensor analog to digital section.
    Added more specific net classes to be explicit about the logic voltage levels of the different boards.
    Added 3.3V to 5V logic conversion for the I2C bus.
    [PolarTableShield.brd, PolarTableShield.sch]
2018-10-10 Layed out existing design. Added headers for all pins.
    [PolarTableShield.brd, PolarTableShield.sch]
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2018-10-10 Labels and layouts
    [PolarTableShield.sch]
2018-10-11 WIP
    * Added typedefs for State, Event, PinID and a few others.
    * Moved to using headers for all but the base file.
    * Created the events file and types for inter module coms.
    * Unified the helpers
    * Prototype I2C snippet file
    * Created base keywords file (Haven't seen it working yet)
    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
2018-10-11 Split the LED button into it's own header
    Rebuilt the event structure. Added the ability to auto transition after a timer.
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2018-10-11 Code tidy up and simplification.
    Created templated struct for packing data for sending to on the wire.
2018-10-12 Layout and added frame.
    Added status lights.
    Matched trace lengths on the I2C bus.
    Added logo.
    Fixed up I2C connection on the SX1509 pins.
    Added better labels and descriptions.
    [PolarTableShield.brd, PolarTableShield.sch]
2018-10-12 Added the sparkfun design for the Pro Mini to reference.
    [Arduino-Pro-Mini.brd, Arduino-Pro-Mini.sch]
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2018-10-15 Added FSM to the project.
    Renamed all of the existing State typedefs to State2.
    Upgraded Button to use FSM.
    Upgraded ButtonLEN to use FSM.
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2018-10-16 Move work on the event system.
    Fixed a bunch of warnings.
    Split the file into a cpp and header.
    Overloaded the triggers so we don't have to create new Event objects all the time.
    [PolarTable.ino]
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2018-10-16 Moved the LED drive connection onto hardware SPI pins.
    [PolarTableShield.brd, PolarTableShield.sch]
2018-10-16 Worked on the timed events.
    Timed events are now killed after run.
    Changed the timer checks to only happen once we reach the min timer time.
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2018-10-17 Added a LED for error signals
    [PolarTableShield.brd, PolarTableShield.sch]
2018-10-17 Added a handler to receive error signal and turn on the error LED.
    [Motors.h, PolarTable.ino]
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2018-10-17 Moved the relative encode switches to the Arduino
    Added hardware XOR on the relative encode switches.
    Combined the main switch and encoder interrupt connections.
    [PolarTableShield.brd, PolarTableShield.sch]
2018-10-17 Removed the error LED as I needed the pin :(
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2018-10-17 Worked on the header include flow.
    Moved the external library includes mostly out of the main ino and into the modules using the functions.
2018-10-18 New blinking error LED event
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2018-10-18 Moved the pins to be more efficient.
    Put the rotory encoder signals onto D8 & D9 so they are on digital pin bank B in the lowest two bits. This can save a cycle shifting the data into position.
    [PolarTableShield.brd, PolarTableShield.sch]
2018-10-18 Rebuilt the relative encoder to be faster.
    Now using ideal pins on arduino rather than SX1509
    Replaced digitalRead calls with direct register reads.
2018-10-21 Got the events flowing again
    Went back to using event struct to send the data around.
    Created a generic template struct to bridge between the event system and the FSM
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2018-10-22 Remove the Arduino headers and just integrated the atmega328 directly
    Added atmega328 chip
    More indicator lights
    Added 3.3v supply
    ICP and SPI headers
    [PolarTableShield.brd, PolarTableShield.sch]
2018-10-23 Fix a couple of compiler warnings
2018-11-02 Updates to the interrupt logic
    The timer button and the relative encoder signals now OR together.
    The relative encoder now has an XORed interrupt trigger.
    Replaced the main diode with something a bit smaller.
    Replaced the 3.3v regulator chip.
    Added buffers to the encoder signals.
    Changed the crystal setup on the atmega chip.
    [PolarTableShield.brd, PolarTableShield.sch]
2018-11-05 Thinking about splitting out the power into a separate board.
    [PolarTableShield.brd, PolarTableShield.sch, Power.brd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]
2018-11-05 Re-enabled the error LED code
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2018-11-06 Moving to program memory based strings. Link stage is failing.
    [PolarTable.ino]
2018-11-06 Got the debug string macros working.
    Downgraded board version to 1.6.21 to fix linker issue.
    Removed the dummy SX1509 header.
    [PolarTable.ino]
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2018-11-07 Didn't save any memory.
    [Event.ino]
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2018-11-08 Pin swap to match hardware
2018-11-08 Updated motor setting pins to match code.
    [PolarTableShield.brd, PolarTableShield.sch]
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2018-11-15 Splitting out the I2C functions to avoid confusion.
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2018-11-18 WIP: Created mock pigpio to write test data onto the pigpio interface.
    I needed some tools for visualizing I2C traffic and making it consistent and slow.
    Wanted to make a faster feedback loop that was all in python.
    Got starts and stops working.
    Got addresses working.
    There is a bug, a 1 is getting inserted into the data MSB. Maybe an ack?
    [bb_i2c_peripheral.py, pigpio_mock.py]
2018-11-19 Created a monitor for our signals.
    Using UDP to send pin states from the main tool across to a separate watcher.
    Also started using curses to better manage printing the streams of data.
2018-11-20 WIP on I2C
    Added optional tags to data logging.
    Changed around mock so the stop events can fire properly.
    Moved to json based packets for data transmission.
    Moved to a queue for receiving data so we don't drop packets.
    Packets are now time-stamped on arrival.
    Hooked up the offset and limits to the window size so we don't overflow the UI.
    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
2018-11-20 Moved a bunch of display code into a Window class.
    Tidied up the calculations for stream width.
    Fixed up the data bit stream.
    Fined up the accumulated hex data display.
    [pigpio_monitor.py]
2018-11-21 Fixed display bug that stopped the borders building until resize
    [pigpio_monitor.py]
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2018-11-26 Created a Mega based layout, split motor shield into it's own board.
    [PolarTableMegaShield.brd, PolarTableMegaShield.sch, PolarTableMotorShield.brd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]
2018-11-26 Changed the connector to be 6x2 so the shift reg could run at 3.3V
    [PolarTableMegaShield.brd, PolarTableMegaShield.sch, PolarTableMotorShield.brd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]
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2018-12-03 Fixing up compile errors
    [Motors.h]
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2018-12-04 Fixing up the FSM state driver.
    [Motors.h, PolarTable.ino]
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2018-12-12 WIP: Fixing compile errors
    [PolarTable.ino]
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2018-12-14 Fixing crash in setup phase.
    [PolarTable.ino]

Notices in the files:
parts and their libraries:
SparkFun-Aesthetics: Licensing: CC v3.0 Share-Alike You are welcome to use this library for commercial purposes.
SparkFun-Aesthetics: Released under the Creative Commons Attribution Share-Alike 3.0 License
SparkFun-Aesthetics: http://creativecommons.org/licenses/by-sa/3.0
